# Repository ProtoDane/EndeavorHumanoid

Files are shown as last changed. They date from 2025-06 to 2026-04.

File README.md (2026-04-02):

# Endeavor II - 3D Printed Humanoid Robot
Endeavor II is a small scale humanoid robot with a height of 50 cm and 4 kg weight.  This robot is inspired by the Japanese robotics competition ROBO-ONE, and is capable of agile movements, combat-oriented sequences, and dance moves.  It is also designed to be fully 3D printed off standard commercial machines and use commercial off the shelf electronics.  Depending on shipping fees, the cost of this robot ranges between $600 to $800.

Endeavor II is fully open source.  In this repository you will find everythign you need to build and customize your own Endeavor: STEP, STL, and code files.

<p align="center">
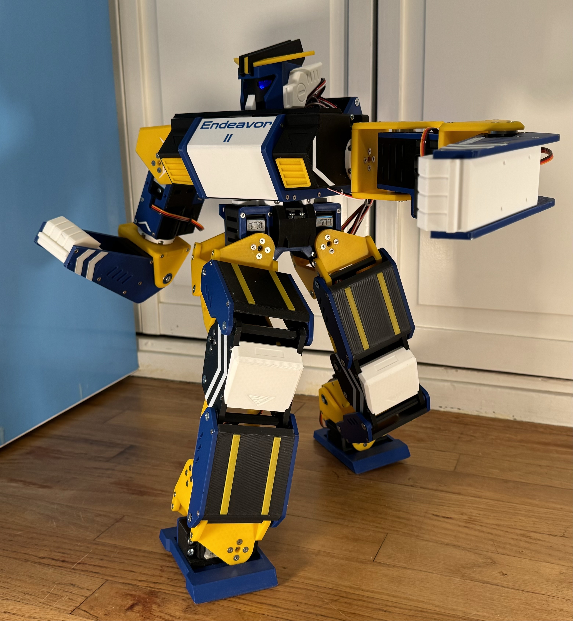
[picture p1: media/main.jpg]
  
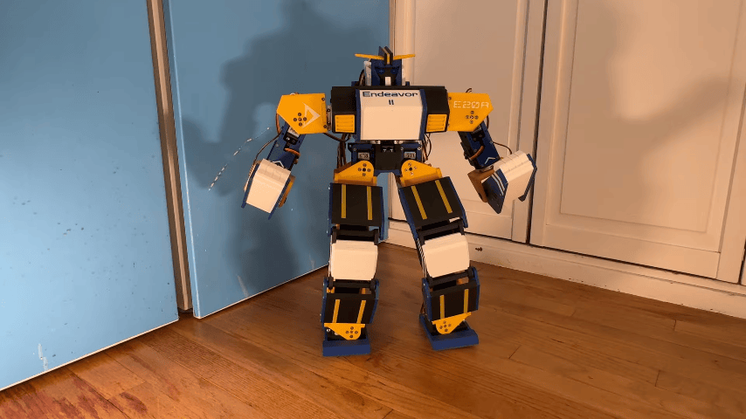
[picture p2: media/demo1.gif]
  
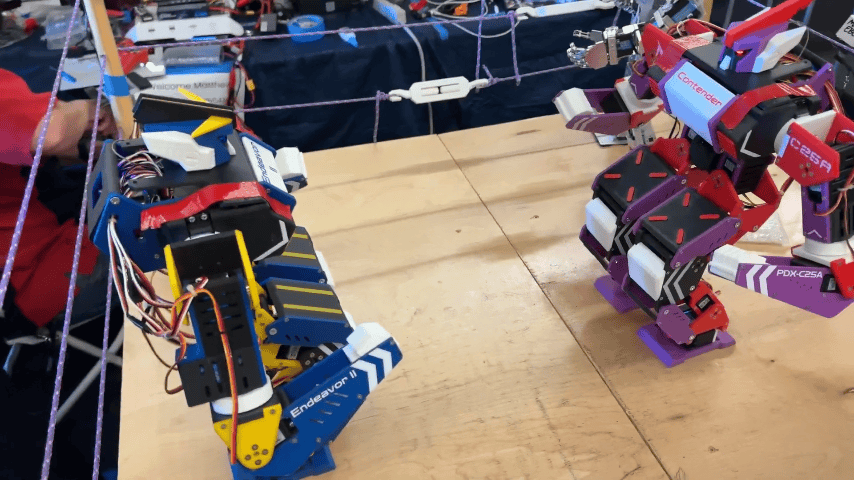
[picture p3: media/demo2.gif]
    
</p>

## Latest Update: (DATE)
**Initial Open Source Release!!!**

Version 01: Initial Open Source Release

See the [CHANGELOG.md] for full update history.

## Getting Started
### Installing this repository

Clone this repository to your local machine:
```bash
git clone
git submodule update --init --recursive
```

### Hardware Assembly

1. It is recommended to do the servo calibration before assemblying the robot.  Refer to [ServoCalibration.pdf] for instructions on how to do this.

1. Refer to [AssemblyDoc.pdf] for hardware assembly instructions.

1. Standard for wiring is in the works, but for now you can refer to the following wiring diagram:

<p align="center">
  
</p>

### Software Setup
Refer to [SoftwareSetup.pdf] for software setup instructions

## To-Do List
- [ ] Finish documentation
- [ ] ESP32 controller optimization (phase out ArduinoIDE code)
- [ ] ESPNOW support for PC teleoperation
- [ ] Idk do some cool stuff

## Support Me!

This project was created by ProtoDane Robotics.  If you like this project and wish to support my future works, I would really appreciate if you followed me on my [YouTube channel]!

If you wish to discuss this project with me, I have a [Discord server].

[STARTHERE.md]:./STARTHERE.md
[CHANGELOG.md]:./CHANGELOG.md
[Discord server]:https://discord.gg/Gm2sCxpUSx
[ServoCalibration.pdf]:./docs/ServoCalibration.pdf
[AssemblyDoc.pdf]:./docs/AssemblyDoc.pdf
[Youtube channel]:https://www.youtube.com/@ProtoDane

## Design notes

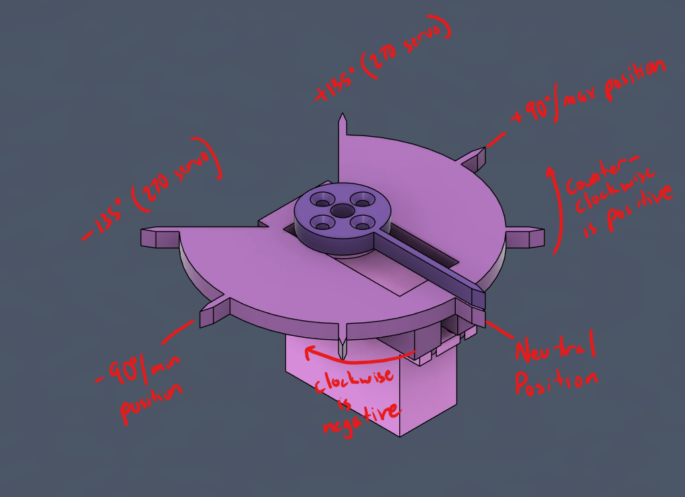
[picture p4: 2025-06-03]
media/servo_jig_annotate.png

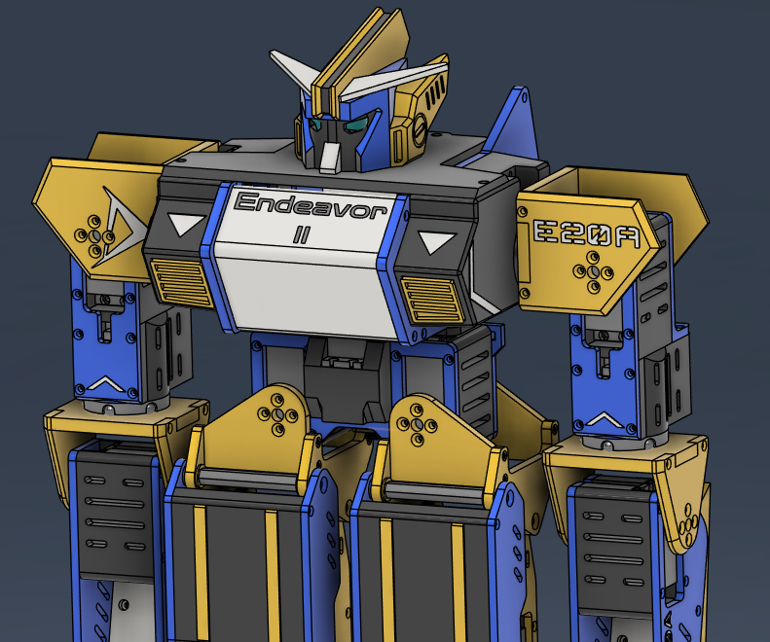
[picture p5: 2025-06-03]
media/Endeavor2_CAD.png

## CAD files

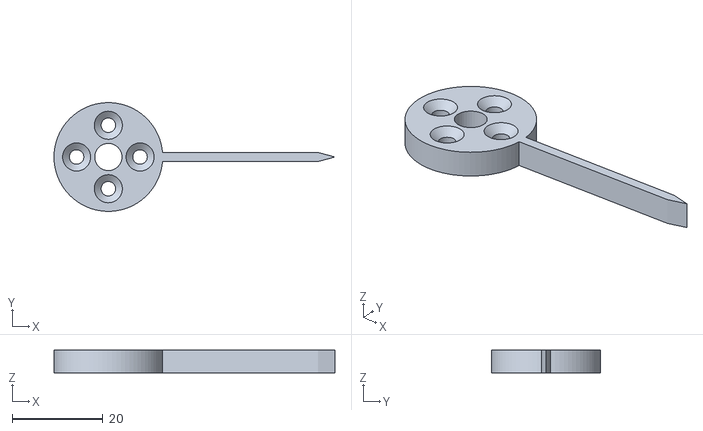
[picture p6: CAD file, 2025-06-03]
firmware/servo_calibration/ServoDial.stl
62.0 x 24.0 x 5.00

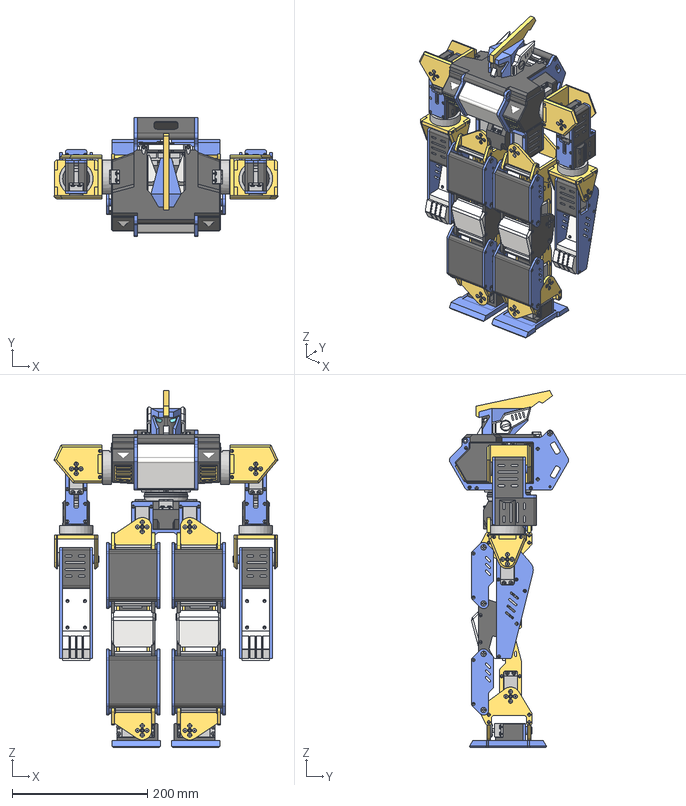
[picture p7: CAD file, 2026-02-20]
hardware/step files/EndeavorII-v1.step
331.0 x 176.6 x 527.7 mm
ElbowBaseBracket x 2
ElbowServoFlange x 2
ElbowBearingFlange x 2
91420A222_Steel Phillips Flat Head Screws x 38
8x14x4 Bearing x 12
ShaftPlug x 12
92010A020_NO THREADS_Passivated 18-8 Stainless Steel Phillips Flat He ad Screw x 241
92010A118_Passivated 18-8 Stainless Steel Phillips Flat Head Screw x 96
91290A111_Alloy Steel Socket Head Screw x 17
DS3235 Servo - Metal Horn x 17
ServoHousingA x 6
92005A118_NO THREADS_Steel Pan Head Phillips Screw x 68
FistBlock x 2
LeftForearmInnerPlate
LeftForearmOuterPlate
LeftShoulderRearFlange
ShoulderBracketBase x 2
LeftShoulderFrontFlange
BicepServoHousing x 2
ShoulderServoHousing x 2
BicepBracket x 2
RollsA x9 x 4
RollsB x9 x 4
ArmSlew-OuterRace x 4
ArmSlew-InnerBottom x 4
ArmSlew-InnerTop x 4
BicepPlate x 2
RightForearmOuterPlate
RightForearmInnerPlate
RightShoulderRearFlange
RightShoulderFrontFlange
TorsoBackPlate
TorsoLeftPlate
TorsoRightPlate
TorsoBottomPlate
RightVent
ShoulderHousingR
RightVent(Mirror)
ShoulderHousingL
TorsoTopCover
TorsoFrontCover
HeadBase
Helmet
Chinpiece
SidepieceL
SidepieceR
Horn
ElectronicsCarriage
Servo2040
Youngneer Single Chsnnel 5V Relay
IMU Mount
Zeee 2S Hard 5200mAh
switch-step
pcb
chip (1)
en button
boot button
usbport
Board
10uF x 2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

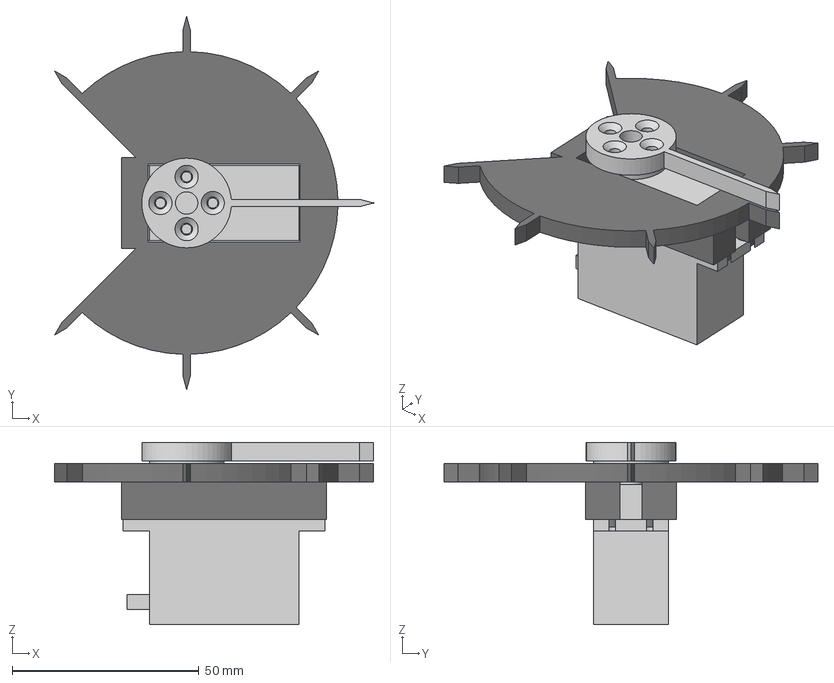
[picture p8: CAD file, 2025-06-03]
firmware/servo_calibration/ServoCalibrationJig.step
85.4 x 100.0 x 48.7 mm
DS3235 Servo - Metal Horn
ServoMount
ServoDial

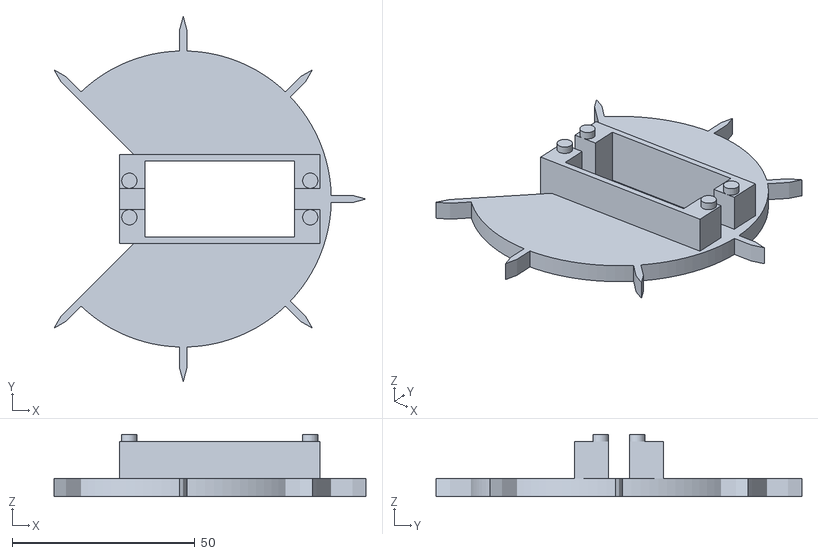
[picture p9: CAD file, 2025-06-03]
firmware/servo_calibration/ServoMount.stl
85.4 x 100.0 x 17.0

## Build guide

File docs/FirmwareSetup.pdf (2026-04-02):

# Programming Instructions

## For the Endeavor Humanoid by ProtoDane Robotics

## Requirements

- VSCode with PlatformIO
- (Optional) VS Code + Arm GNU Toolchain (mingw32) for working with the Servo2040; binary files and the communication protocol have been provided.

## 1: Flash the Servo 2040

Unless you want to add custom functionality, the binary files for the Servo 2040 have been provided to make the Pico SDK installs optional (this document does not cover the Servo2040 source code).

1. Download the binary file from the GitHub repository under servo2040/firmware/binaries. If using the Servo2040 without IMU, download servo2040_client.uf2. Otherwise, use servo2040_client_imu.uf2.
2. Plug in the Servo 2040 board to a computer via USB-C cable while holding down the BOOT button. Within a few seconds a file storage for the 2040 should pop up on the desktop.
3. Drag the .uf2 file into the 2040’s file storage. The file storage should disappear and LED lights should start coming up.

## 2: Configure the ESP32 code and upload

1. Open firmware/esp32_controller in VSCode and wait for PlatformIO to initialize and configure the project.
2. Find the MAC address of the Bluetooth controller you want to use for your robot and set that as the value of CTRL_MAC.

a. The MAC address of the Bluetooth controller can be found by running the ‘Controller’ sketch within the Bluepad32 Examples folder.
b. Upload the sketch to the ESP32 (or a spare one if you have it). Open the serial terminal (9600 baud rate).
c. Set your controller to pairing mode and wait for the connection message with the MAC address in the terminal.
3. Open platformio.ini and scroll down to [env:my_robot]. This is where you will configure your robot parameters; if you have multiple robots or different configurations, you should copy the lines including and below line 20.
a. CTRL_MAC: MAC Address of Bluetooth controller
b. IMU_CONFIG: 0 = IMU Disabled | 1 = BNO-055 | 2 = BNO-08X
c. SERIAL_DEBUG_MODE: If set true, disables all motor functions to safely troubleshoot over USB cable
d. FALL_PROTECTION_ENABLED: If set true, relay will automatically switch off when IMU_TIP_THRESHOLD (config.h) is reached
e. ULT_LOCK: If set true, will disable the tumble “ultimate” move for safety
f. CONFIG_FILE: If uncommented, will use the specified file name instead of robotInfoDefault.h
4. Navigate to robotInfoDefault.h (or your copied file). Fill in the servoStruct definitions with the servo calibration values that you recorded. The formatting is as follows: {min, mid, max, is180}, where is180 is a boolean value that is true of the servo is a 180-degree servo.
a. Example:

const servoStruct s_torso = {515, 1458, 2397, false}; | // TORSO
const servoStruct s_ra1 = | {510, 1495, 2397, false}; | // RIGHT ARM SHOULDER BASE
const servoStruct s_ra2 = | {543, 1505, 2413, false}; | // RIGHT ARM SHOULDER SWING
const servoStruct s_ra3 = | {592, 1495, 2404, true}; | // RIGHT ARM BICEP SWIVEL
const servoStruct s_ra4 = | {593, 1493, 2385, true}; | // RIGHT ARM ELBOW
const servoStruct s_rl1 = | {592, 1512, 2405, true}; | // RIGHT LEG THIGH
const servoStruct s_rl2 = | {588, 1490, 2372, true}; | // RIGHT UPPER LEG
const servoStruct s_rl3 = | {643, 1550, 2432, true}; | // RIGHT LOWER LEG
const servoStruct s_rl4 = | {587, 1493, 2405, true}; | // RIGHT LEG ANKLE
const servoStruct s_la1 = | {505, 1457, 2409, false}; | // LEFT ARM SHOULDER BASE
const servoStruct s_la2 = | {550, 1509, 2453, false}; | // LEFT ARM SHOULDER SWING
const servoStruct s_la3 = | {622, 1530, 2480, true}; | // LEFT ARM BICEP SWIVEL
const servoStruct s_la4 = | {622, 1533, 2440, true}; | // LEFT ARM ELBOW
const servoStruct s_ll1 = | {597, 1500, 2410, true}; | // LEFT LEG THIGH
const servoStruct s_ll2 = | {685, 1580, 2470, true}; | // LEFT UPPER LEG
const servoStruct s_ll3 = | {567, 1522, 2437, true}; | // LEFT LOWER LEG
const servoStruct s_ll4 = | {591, 1520, 2428, true}; | // LEFT LEG ANKLE

Note, you shouldn’t need to change the servoCluster mapping unless your servo wiring is different from the Wiring doc.

5. Plug in the ESP32 to your computer. Compile the project and upload.

## Sanity Checklist

After a few seconds the LED bar on the Servo2040 flashes green After a few seconds the LEDs inside the robot’s head flashes Pairing the Bluetooth controller to the robot is successful Pressing the Home Button brings the robot to its idle position

## Appendix A: Servo2040 Communication Protocol

- Servo2040 communicates with the ESP32 over UART1 at a baud rate of 115200
- Upon startup, the LED bar will light up to signal certain stages of the initialization process. The LED bar will flash all green to indicate that it is ready for operation.
- The Servo2040 will yield until the ESP32 sends a handshake message of 0b01101001 or a hexadecimal of 0x69 (this was not intentional, I swear).
- The Servo2040 waits for the ESP32 to receive a command byte, in which the leading 4 bits are known as the preamble; each value used to indicate what to send back to the

ESP32, however this feature has been deprecated. The Servo2040 will recognize the following bytes:
- 0x08
- 0x09
- 0x0F
- The trailing 4 bits of the command bit is the command code, and each value indicates an action the Servo2040 executes:
- 0x0F | CMD_ENABLE: Allows transmission of PWM signals to the servos.
- 0x01 | CMD_DISABLE: Discontinues sending PWM signals to the servos.
- 0x02 | CMD_LED: Controls the LED bar
■ The following byte controls which LEDs are lit. For instance, if the byte value is 0b10011, this indicates that LEDs 1, 2, and 5 are lit.
■ Example full message: (0x0F << 4 | CMD_LED) (0b10011)
- 0x07 | CMD_PULSE: Sends PWM signals to all servos
■ The command byte is followed by 36 bytes, each pair of bytes representing the target PWM pulse for a specific servo for a total of 18 actuators.
■ The pulse values must be between 500 and 2500 per manufacturing specifications. If the pulse value falls outside this range the servo will be ignored; this is implemented such that the user can control which servos need to be actuated.
■ Example message: (0x0F << 4 | CMD_PULSE) (10) (50) (0) (0) (15) (0)
(15) (0) (15) (0) […]
- Sets SERVO1 to 1050, ignores SERVO2, SERVO3-SERVO18 to 1500
- 0x06 | CMD_PULSE_DELAY: Moves all servos from current position to target
position within a specified time delay.
■ The command byte is followed by two bytes indicating the time delay in milliseconds, then the 36 bytes for the 18 servos.
■ Example message: (0x0F << 4 | CMD_PULSE_DELAY) (20) (50) [Same
parameters as CMD_PULSE]
- Moves all servos to desired position after 2050 ms
■ Note: speed of servos depend on the most recent pulse or delayed pulse command

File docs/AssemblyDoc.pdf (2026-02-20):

# Endeavor

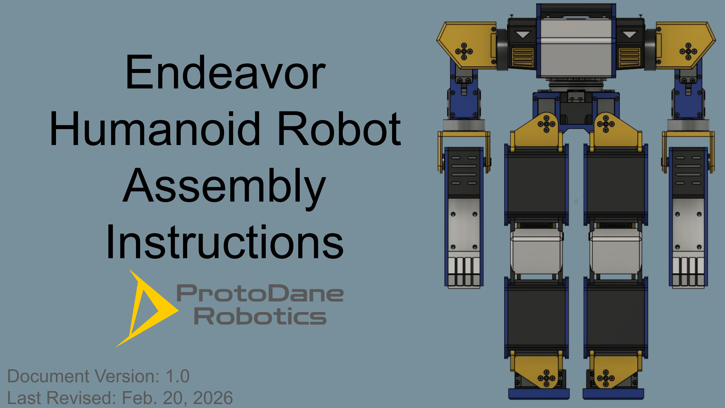
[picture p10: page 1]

# Humanoid Robot Assembly Instructions

# ProtoDane Robotics

## Document Version: 1.0 Last Revised: Feb. 20, 2026

# Notes

## - Refer to servo calibration instructions for DS3235 servos. All servos should be calibrated before starting assembly. Do not remove or rotate the servo

disc to ensure servo joints are set properly when powered.

## - This assembly does not contain heat inserts. As such, all fasteners should be tightened properly, either by hand or motorized tool. It is up to you to ensure that all fasteners are secured and not overtightened that it

destroys the printed hole.

## - Read each step carefully. You are responsible for proper assembly, safe tool handling, and any risks associated with this project. If you have any

questions, please reach out on the ProtoDane Discord server.

# 01: Ankle Servo Assembly

No. | Part Name | Qty
1 | LeftAnkleServoHousing | 1
2 | RightAnkleServoHousing | 1
3 | LeftAnkleBracket | 1
4 | RightAnkleBracket | 1
5 | DS3235 Servo | 2
6 | M3x8 Pan Head Screw | 8
7 | M2.5x10 Flat Head Screw | 6

7

6

5

2

1

3

4

# 02: Foot Mounting

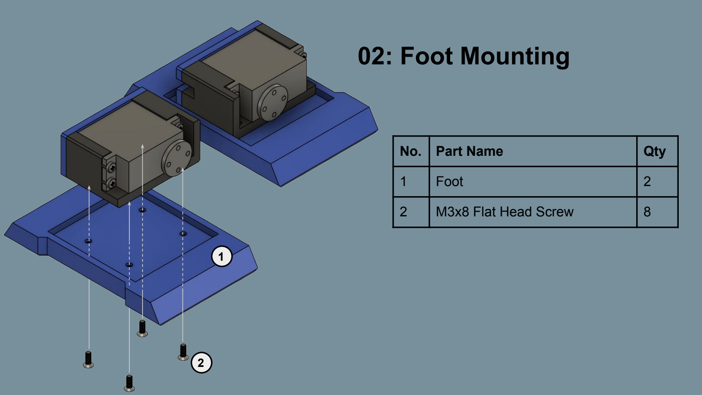
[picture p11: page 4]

No. | Part Name | Qty
1 | Foot | 2
2 | M3x8 Flat Head Screw | 8

1

2

# 03: Ankle Bracket Assembly

## *Repeat step

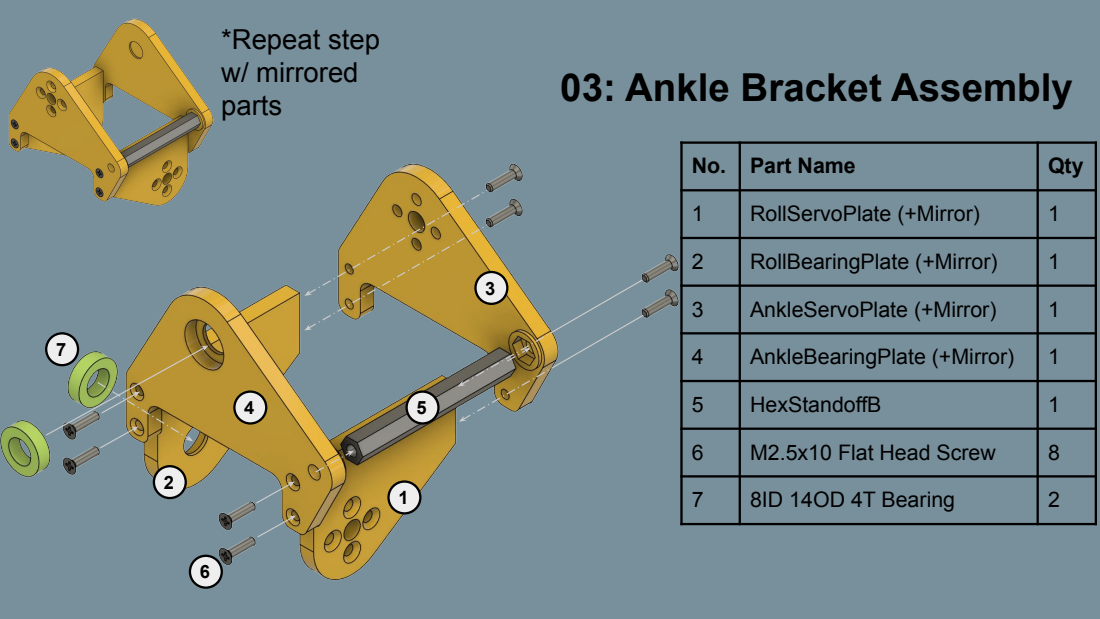
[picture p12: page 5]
Part Name; Qty; w/ mirrored parts

1 | RollServoPlate (+Mirror) | 1

2 | RollBearingPlate (+Mirror) | 1

3 | AnkleServoPlate (+Mirror) | 1

4 | AnkleBearingPlate (+Mirror) | 1

5 | HexStandoffB | 1

6 | M2.5x10 Flat Head Screw | 8

7 | 8ID 14OD 4T Bearing | 2

# 04: Thigh Bracket Assembly

## *Repeat step w/ mirrored parts

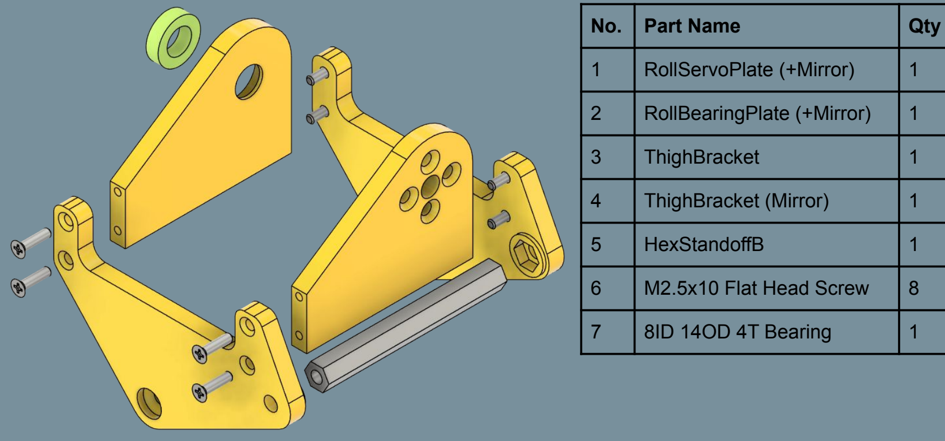
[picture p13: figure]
Part Name; Qty; RollServoPlate (+Mirror); RollBearingPlate (+Mirror); ThighBracket; ThighBracket (Mirror); HexStandoffB; M2.5x10 Flat Head Screw; 8ID 14OD 4T Bearing

# 05: Front Leg Guards

No. | Part Name | Qty
1 | FrontLinkage | 1(x4)
2 | FrontLinkage(Mirror) | 1(x4)
3 | FrontLinkageCover | 1(x4)
4 | M2.5x10 Flat Head Screw | 4(x4)

## *Build x4

1

2

3

4

# 06: Knee Assembly

## *Repeat step

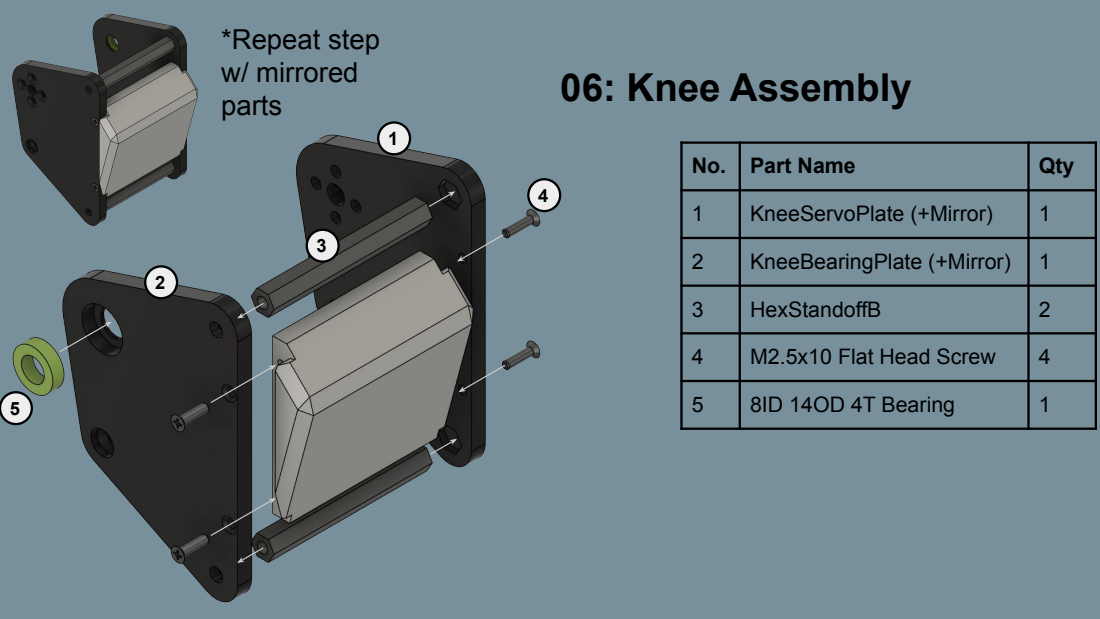
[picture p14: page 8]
w/ mirrored parts; Part Name; Qty 1; KneeServoPlate (+Mirror); KneeBearingPlate (+Mirror); HexStandoffB; M2.5x10 Flat Head Screw; 8ID 14OD 4T Bearing

# 07: Servo Module A

## *Build x6

No. | Part Name | Qty
1 | ServoHousingA | 1x6
2 | DS3235 Servo | 1x6
3 | M3x8 Pan Head Screw | 4x6
1

2

3

# 08: Servo Leg Assembly

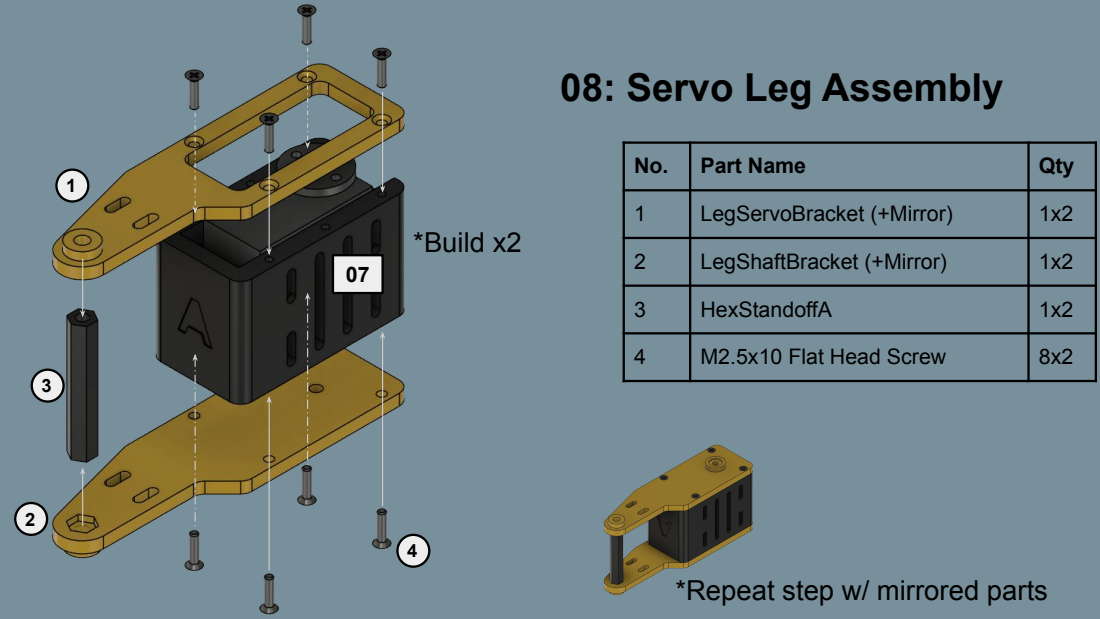
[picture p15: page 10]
*Build x2

No. | Part Name | Qty

1 | LegServoBracket (+Mirror) | 1x2

2 | LegShaftBracket (+Mirror) | 1x2

3 | HexStandoffA | 1x2

4 | M2.5x10 Flat Head Screw | 8x2

*Repeat step w/ mirrored parts

# 09a: Lower Leg Assembly

No. | Part Name | Qty
1 | M3x8 Flat Head Screw | 8
2 | M3x6 Socket Head Screw | 2
3 | M4x12 Flat Head Screw | 2
4 | ShaftSleeve | 2
Left leg pictured | Repeat step for right leg

08

03

02

1

2

3

4

## Install in the orientation as shown; this is the servo’s zero position

# 09b: Knee Mounting

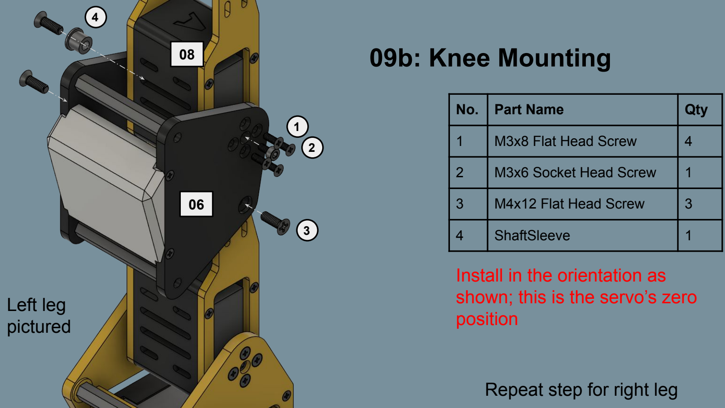
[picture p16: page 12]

No. | Part Name | Qty
1 | M3x8 Flat Head Screw | 4
2 | M3x6 Socket Head Screw | 1
3 | M4x12 Flat Head Screw | 3
4 | ShaftSleeve | 1

## Repeat step for right leg

## Left leg pictured

06

08

1

2

3

4

## Install in the orientation as shown; this is the servo’s zero position

# 09c: Thigh Bracket Mounting

No. | Part Name | Qty
1 | M4x12 Flat Head Screw | 2

## Repeat for right leg

## Left leg pictured

# 09d: Front Linkage Cover Mounting

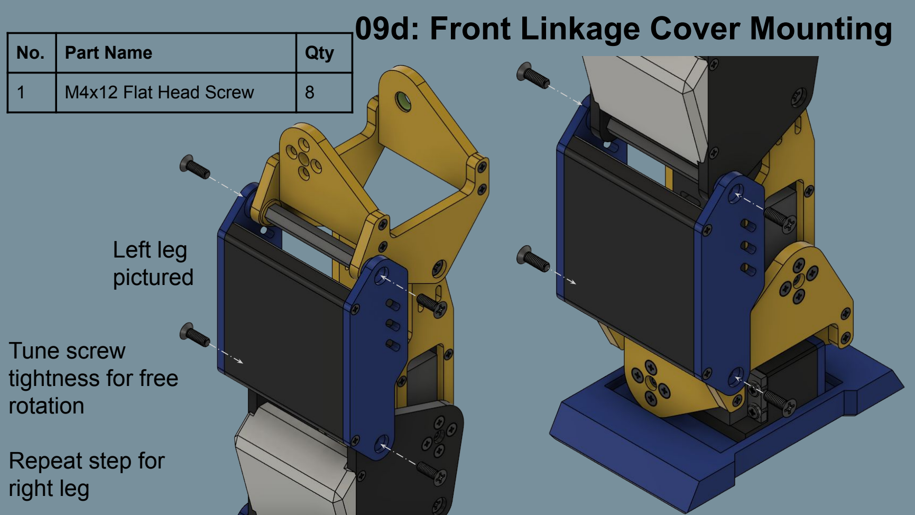
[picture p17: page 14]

No. | Part Name | Qty
1 | M4x12 Flat Head Screw | 8

## Tune screw tightness for free rotation

## Repeat step for right leg

## Left leg pictured

# 09e: Full Leg

Left Leg

Right Leg

# 10: Pelvis Servo Modules

No. | Part Name | Qty
1 | ThighServoHousing | 2
2 | TorsoServoHousing | 1
3 | DS3235 Servo | 3
4 | M3x8 Pan Head Screw | 12

## *Build x2

# 11: Pelvis Assembly

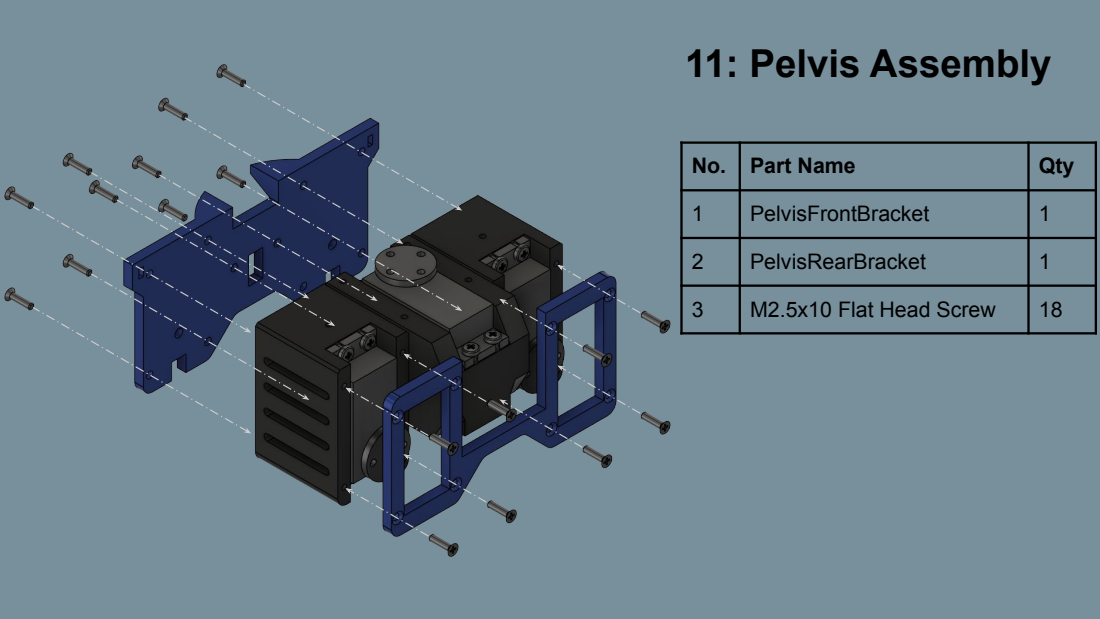
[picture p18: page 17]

No. | Part Name | Qty

1 | PelvisFrontBracket | 1

2 | PelvisRearBracket | 1

3 | M2.5x10 Flat Head Screw | 18

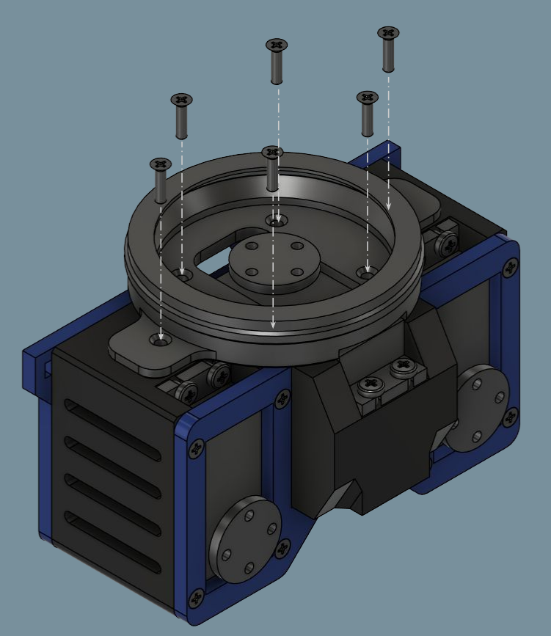
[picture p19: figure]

# 12a: Torso Slew Bearing Mounting

No. | Part Name | Qty
1 | TorsoSlew-OuterRace | 1
2 | M2.5x10 Flat Head Screw | 6

# 12b: Lower Cap + Rollers

No. | Part Name | Qty
1 | TorsoSlew-InnerBottom | 1
2 | SlewRoller | 26

## Drop the InnerBottom piece into the bearing

housing first.

## Alternate slew rollers by 90 degrees (see

image).

# 12c: Upper Cap Mounting

No. | Part Name | Qty
1 | TorsoSlew-InnerTop | 2
2 | M2.5x10 Flat Head Screw | 3
3 | M3x8 Flat Head Screw | 4
4 | M3x6 Socket Head Screw | 1

# 13: Pelvis/Leg Mounting

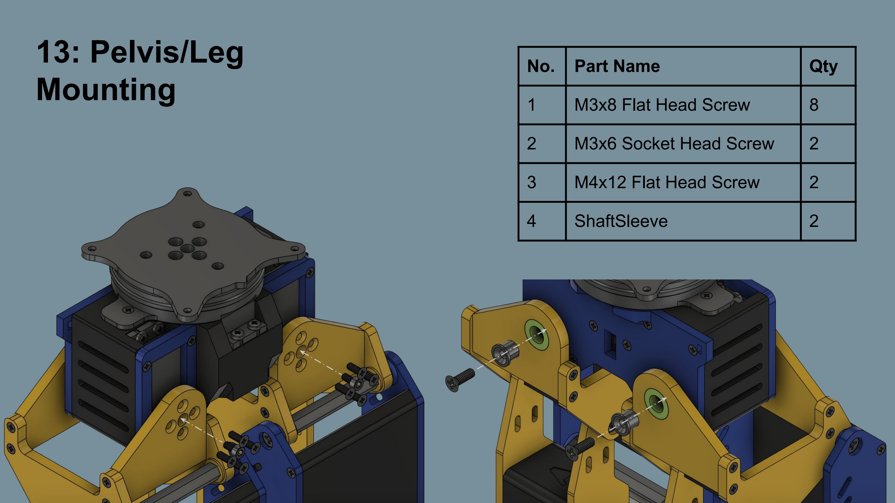
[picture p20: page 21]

No. | Part Name | Qty 1 | M3x8 Flat Head Screw | 8 2 | M3x6 Socket Head Screw | 2 3 | M4x12 Flat Head Screw | 2 4 | ShaftSleeve | 2

# 14a: Chest Servo Housing

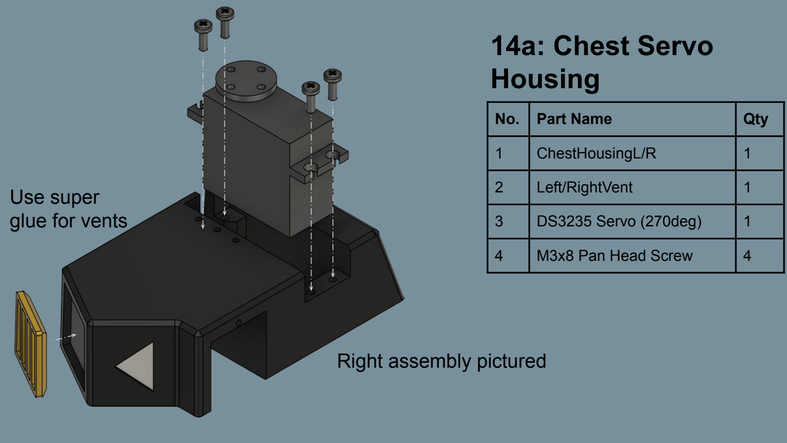
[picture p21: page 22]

No. | Part Name | Qty
1 | ChestHousingL/R | 1
2 | Left/RightVent | 1
3 | DS3235 Servo (270deg) | 1
4 | M3x8 Pan Head Screw | 4

## Right assembly pictured

## Use super glue for vents

# 14b: Arm Slew Bearing Mounting

No. | Part Name | Qty
1 | ArmSlew-OuterRace | 1
2 | M2.5x10 Flat Head Screw | 4*

## *3x screws okay if arranged in triangular pattern

## Right assembly pictured

# 14c: Lower Cap + Rollers

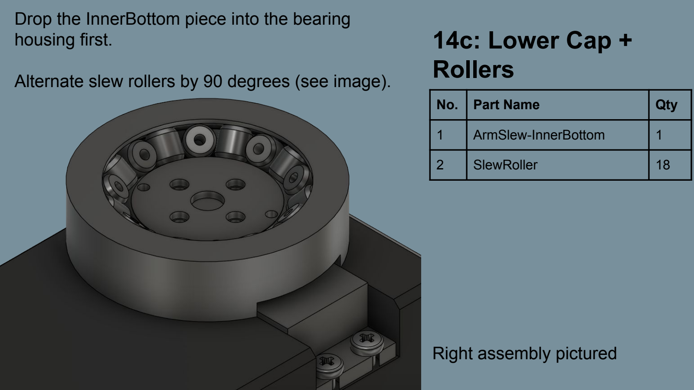
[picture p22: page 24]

No. | Part Name | Qty
1 | ArmSlew-InnerBottom | 1
2 | SlewRoller | 18

## Drop the InnerBottom piece into the bearing

housing first.

Alternate slew rollers by 90 degrees (see image).

## Right assembly pictured

# 14d: Upper Cap

No. | Part Name | Qty
1 | ArmSlew-InnerTop | 1
2 | M2.5x10 Flat Head Screw | 2
3 | M3x8 Flat Head Screw | 4
4 | M3x6 Socket Head Screw | 1

## Right assembly pictured

# 14e: Side Plate Mounting

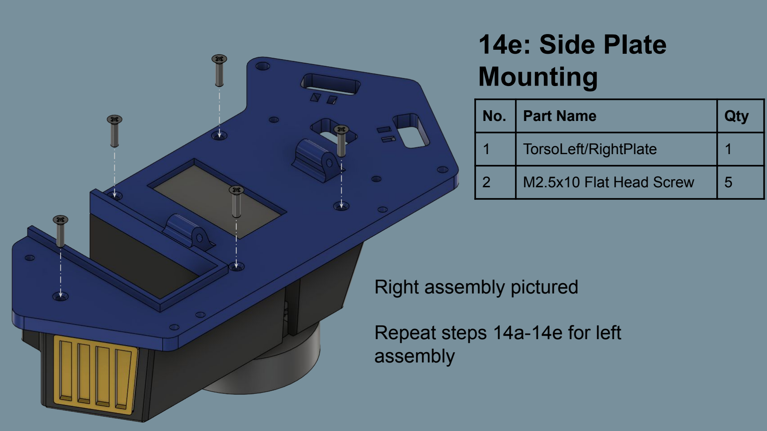
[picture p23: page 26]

No. | Part Name | Qty
1 | TorsoLeft/RightPlate | 1
2 | M2.5x10 Flat Head Screw | 5

## Right assembly pictured

## Repeat steps 14a-14e for left assembly

# 15a: Torso Bottom Plate Mounting

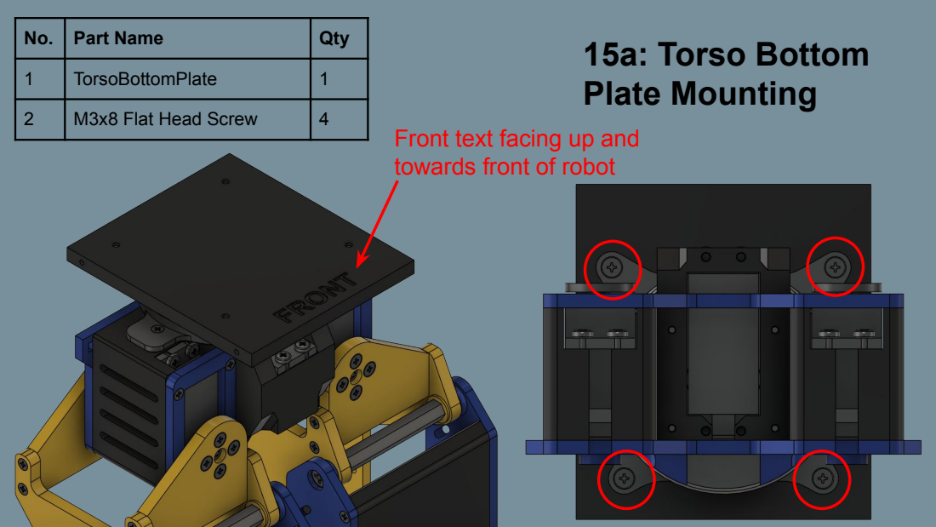
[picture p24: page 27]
M3x8 Flat Head Screw

No. | Part Name | Qty

1 | TorsoBottomPlate | 1

Front text facing up and
towards front of robot

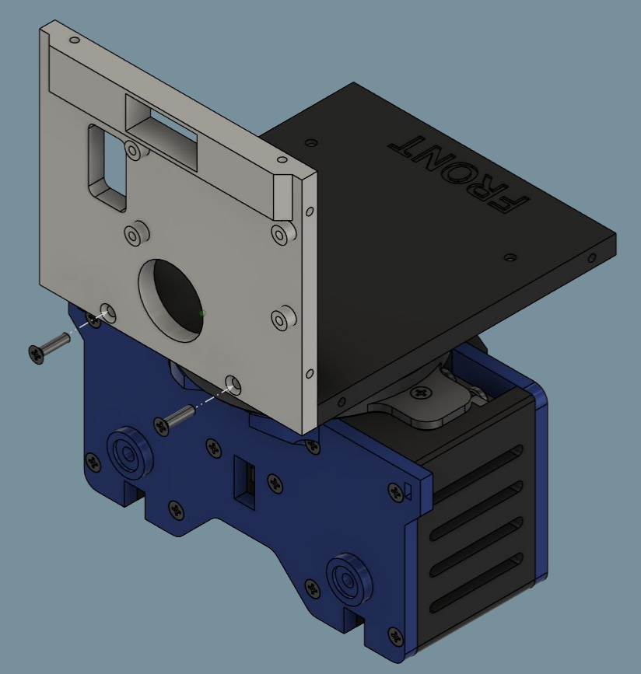
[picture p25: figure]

# 15b: Back Plate Mounting

No. | Part Name | Qty
1 | TorsoBackPlate | 1
2 | M2.5x10 Flat Head Screw | 2

# 15c: Side Assembly Mounting

No. | Part Name | Qty
1 | M2.5x10 Flat Head Screw | 4

## Repeat step for other side

# 15d: Back Cover Mounting

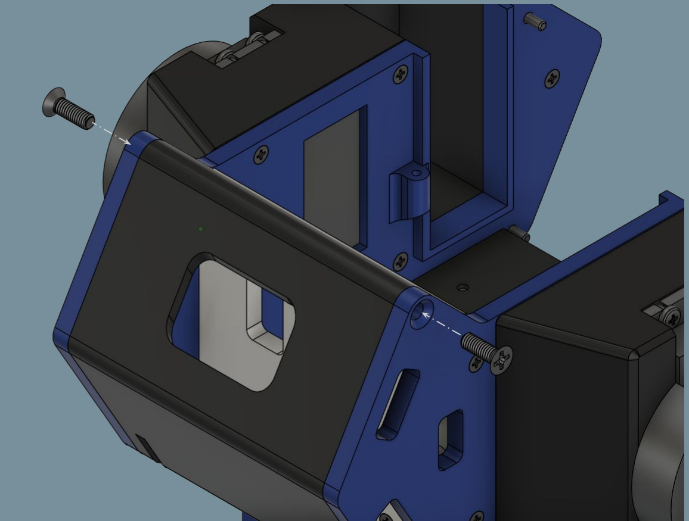
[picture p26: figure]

No. | Part Name | Qty
1 | BackCover | 1
2 | M4x12 Flat Head Screw | 2

# 15e: Front Cover Mounting

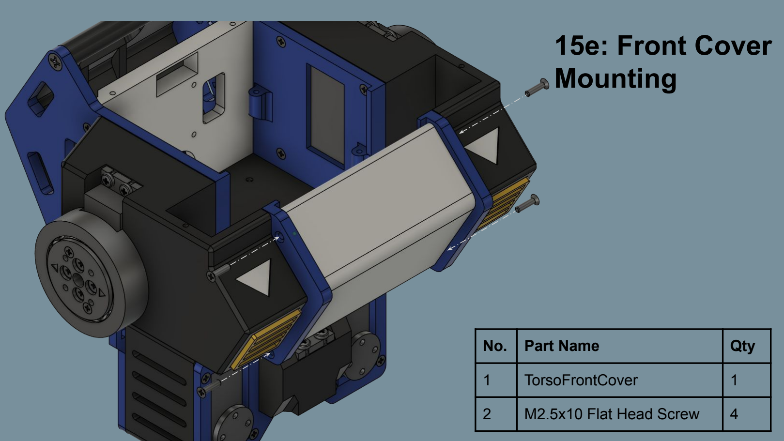
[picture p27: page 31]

No. | Part Name | Qty
1 | TorsoFrontCover | 1
2 | M2.5x10 Flat Head Screw | 4

# 16a: Top Torso Cover

No. | Part Name | Qty
1 | TorsoTopCover | 1
2 | HeadBase | 1
3 | Helmet | 1
4 | Chinpiece | 1
5 | SidepieceL | 1
6 | SidepieceR | 1
7 | Crest | 1

## Use super glue to secure all pieces

# 16b: Top Torso Cover

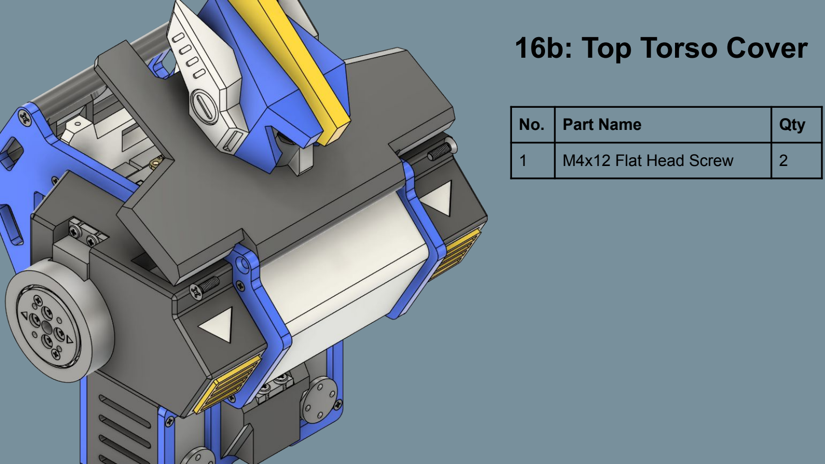
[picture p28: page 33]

No. | Part Name | Qty
1 | M4x12 Flat Head Screw | 2

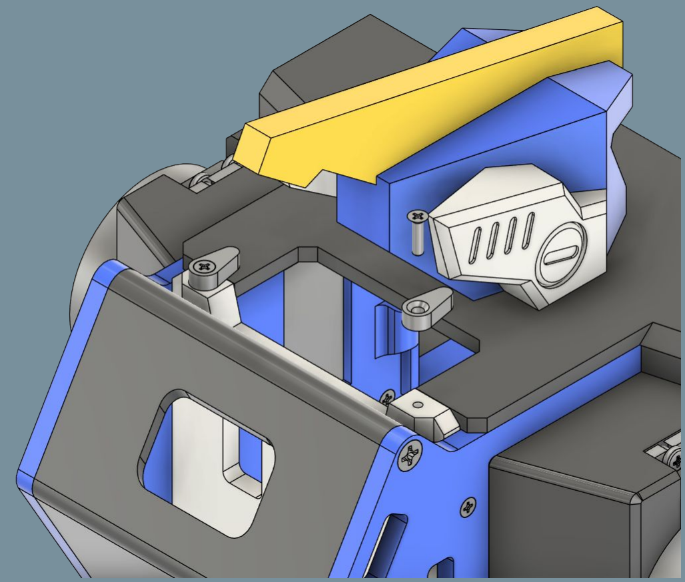
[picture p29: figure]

# 16c: Top Torso Cover

No. | Part Name | Qty
1 | LidStopper | 2
2 | M2.5x10 Flat Head Screw | 2

## Do not overtighten; lid stoppers must be able to

rotate to release the top cover, but not loose.

# 17a: Shoulder Brackets

No. | Part Name | Qty
1 | ShoulderBracketBase | 1
2 | Left/RightShoulderFrontFlange | 1
3 | Left/RightShoulderRearFlange | 1
4 | M2.5x10 Flat Head Screw | 4
5 | 8ID 14OD 4T Bearing | 1

## Right assembly pictured

## Repeat step for left assembly

# 17b: Bracket Mounting

No. | Part Name | Qty
1 | M3x8 Flat Head Screw | 4

## Repeat for other side

## Install in the orientation as shown; this is the servo’s zero position

# 18: Elbow Brackets

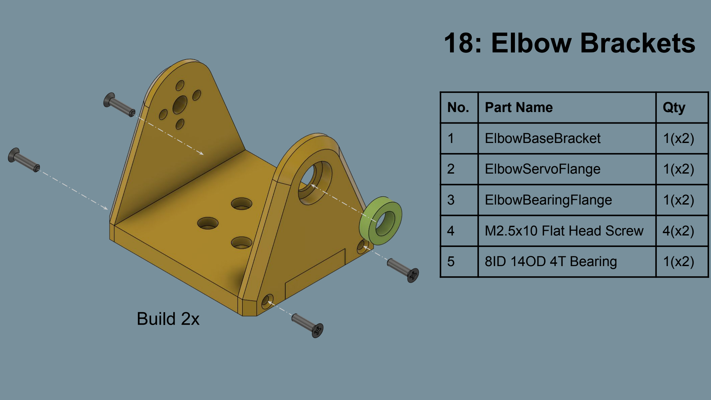
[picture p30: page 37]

No. | Part Name | Qty
1 | ElbowBaseBracket | 1(x2)
2 | ElbowServoFlange | 1(x2)
3 | ElbowBearingFlange | 1(x2)
4 | M2.5x10 Flat Head Screw | 4(x2)
5 | 8ID 14OD 4T Bearing | 1(x2)

## Build 2x

# 19a: Bicep Servo Housings

No. | Part Name | Qty
1 | ShoulderServoHousing | 1
2 | BicepServoHousing | 1
3 | DS3235 Servo | 2
4 | M3x8 Pan Head Screw | 8

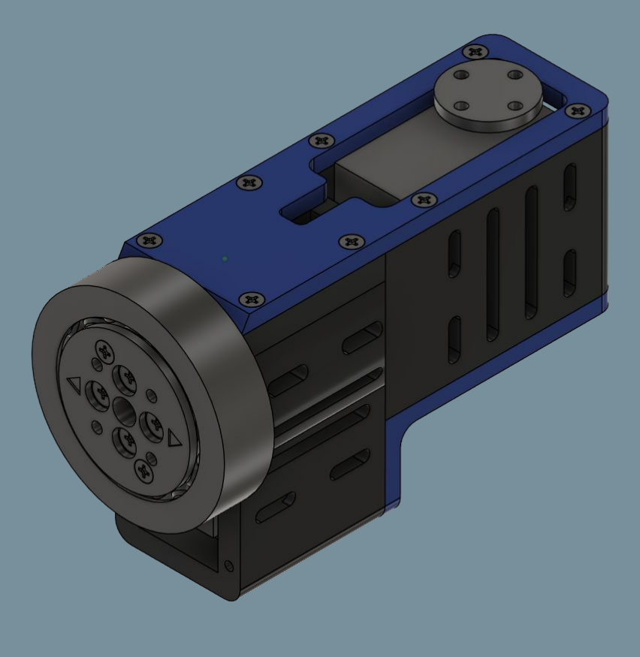
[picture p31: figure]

# 19c: Arm Slew Bearing

## Refer to 14b-14d for detailed steps

## Repeat steps 19a-19c

# 20: Forearm Assembly

No. | Part Name | Qty
1 | Left/RightForearmOuterPlate | 1
2 | Left/RightForearmInnerPlate | 1
3 | Fist | 1
4 | M2.5x10 Flat Head Screw | 14

## Left assembly pictured

## Repeat step for right assembly

# 21a: Elbow Bracket Mounting

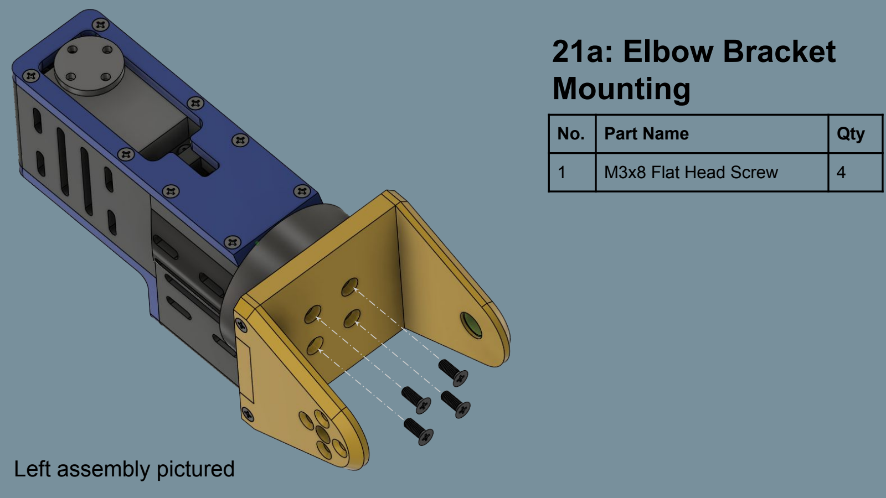
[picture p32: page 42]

No. | Part Name | Qty
1 | M3x8 Flat Head Screw | 4

## Left assembly pictured

# 21b: Forearm Mounting

No. | Part Name | Qty
1 | M3x6 Socket Head Screw | 1
2 | M3x8 Flat Head Screw | 4
3 | M4x12 Flat Head Screw | 1
4 | ShaftSleeve | 1

## Left assembly pictured

## Install in the orientation as shown; this is the servo’s zero position

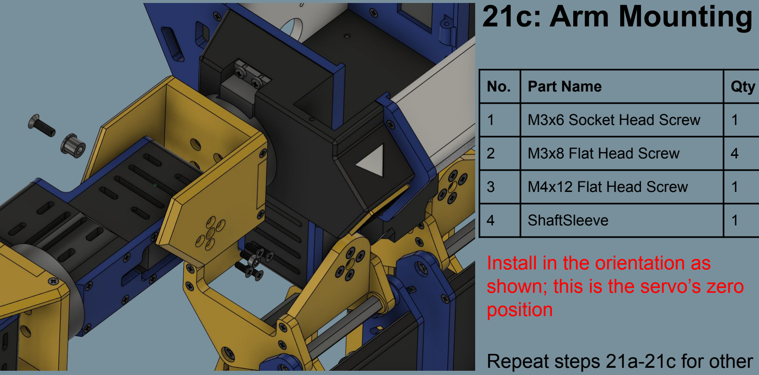
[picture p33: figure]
21c: Arm Mounting; Install in the orientation as shown; this is the servo’s zero position; Part Name; Qty; M3x6 Socket Head Screw; M3x8 Flat Head Screw; M4x12 Flat Head Screw; ShaftSleeve; Repeat steps 21a-21c for other

## side

## ❏ All joints are structurally stable with minimal wobble and resistance (with

exception of motor torque).

## ❏ All joints have been fastened, preferably with reinforcement from a thread

bonding agent (e.g. Loctite) to prevent the servo joint from becoming loose.

## ❏ All structural components are fastened properly with no noticeable gaps

between component interfaces.

# Sanity Checklist

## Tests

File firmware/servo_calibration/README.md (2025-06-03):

# Servo Calibration
I created a simple tool to map the servo PWM values (in microseconds) and map them to angular positions.  This was created because a problem I noticed with Endeavor I was that the servos did not behave the same way.  

When you control a servo, you're often calling servo.write(angle) or an equivalent in other platforms.  What's really going on is that the angle is converted to a pulse width value, which is what's actually sent as a signal to the servo.  However, this convertion is based on an assumed mapping.  Due to things like product quality and manufacturing variations, what may be considered as "45 degrees" may vary by as large as 200 usec pulse difference.

As such, I've designed a jig that consists of a servo dial and an angle measurement indicator.  We use this with the servo_calibration.ino code that I wrote in order to map the intended angles to their actual pulse values.

## Requirements
* Arduino (doesn't matter what model, just needs to work!)
* Serial terminal, PuTTY preferred for live key input
* Servo
* Servo Horn ([Use this] or something of equivalent dimensions)

[Use this]:https://www.amazon.com/dp/B07D56FVK5?ref_=ppx_hzsearch_conn_dt_b_fed_asin_title_2

## Wiring
Nothing too crazy, just hook up the servo to the Arduino's D7 and GND, then wire the servo to an external PSU set to servo voltage (typically 7.4v).



## Instructions
1. Mount 3D printed jig parts to servo, the servo jig goes down from the top (be sure the servo axis is centered), and the servo dial takes in M3 bolts (flathead preferred)
2. Turn on PSU, set voltage to servo range, and connect to servo
3. Plug in USB from your computer to Arduino and open up the serial terminal
4. Follow the instructions in the terminal...
    * Physically adjust the servo horn so that the dial is as close to the neutral position as possible
    * Using the terminal, move the servo so that the dial is at neutral position (~1500 usec); Press SPACE to confirm
    * Using the terminal, move the servo so that the dial is at max position (+90/~2500 usec); Press SPACE to confirm
    * Using the terminal, move the servo so that the dial is at min position (-90/~500  usec); Press SPACE to confirm
    * Run a sanity check by using the terminal to control the servo angle (calibrates to the mapped pulse value automatically).  Check with the jig markings to make sure mostly everything lines up (NOTE: RC servos are inherently unfit for high precision robotics, so expect some error.  At the very least your neutral and min/max values should be accurate)
    * Record the neutral and min/max calibration values (you might want to label the servos as well to keep track).  These will be used to write the robot's firmware.



## Other Notes
* If you're calibrating a 270-degree servo, the instructions are the same, but instead of +/- 90 deg as the min/max, calibrate to the +/- 135 deg marks (one jig mark further).  When running the sanity check, 30 degrees in the terminal correspond to 45 degrees on the servo; the code was made for 180 degrees, which make up the majority of servos, thus didn't justify accommodating for both.

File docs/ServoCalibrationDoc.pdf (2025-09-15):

Last Updated: 2025-09-15

# Servo Calibration Instructions

## For the Endeavor Humanoid Robot by ProtoDane Robotics

## Required Materials:

- Servo Calibration Jig (Servo Dial / Servo Mount)
- DS3235 Servo + Metal Disc
- 2x M3 Screws
- Arduino (Uno, Nano, etc.)
- Power Station

## 1: Prepare the Electronics Setup

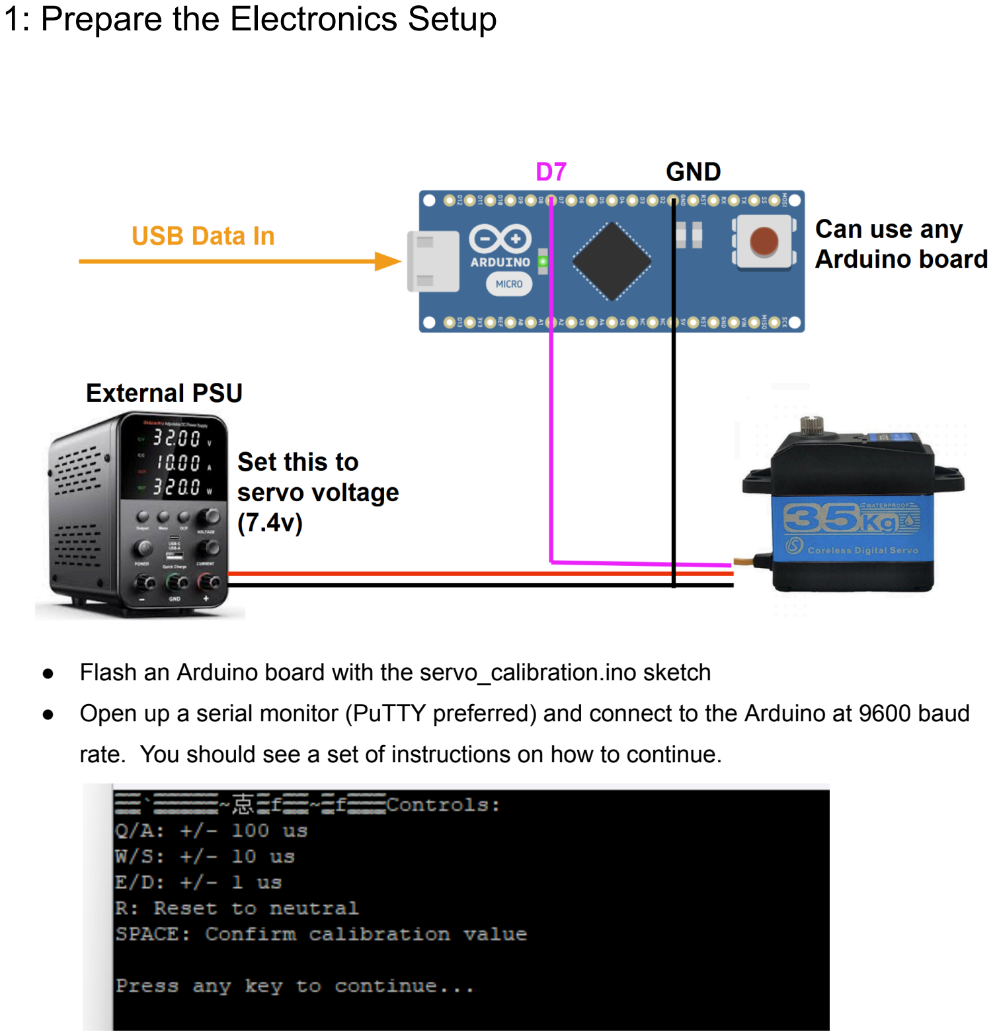
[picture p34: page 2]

- Flash an Arduino board with the servo_calibration.ino sketch
- Open up a serial monitor (PuTTY preferred) and connect to the Arduino at 9600 baud rate. You should see a set of instructions on how to continue.

## 2: Set up Servo in Jig

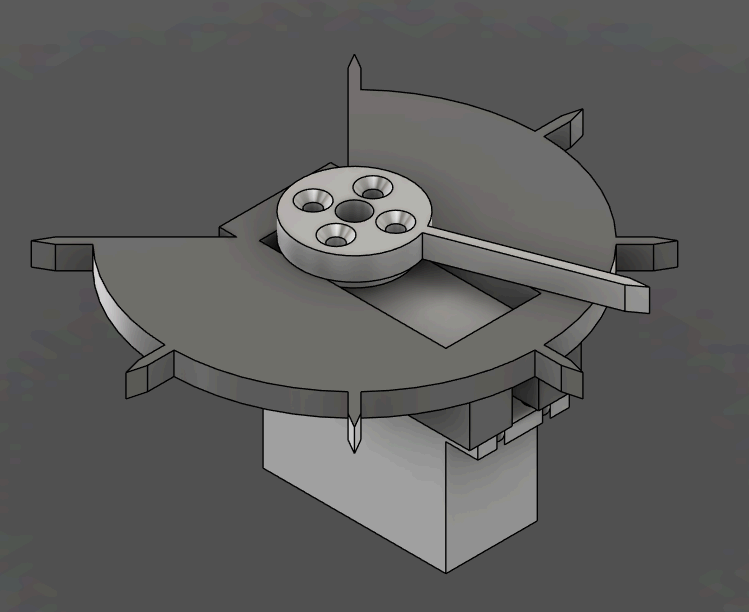
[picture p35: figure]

1. Pop in the ServoMount piece, which should plug into the holes on the mounting tabs of the servo motor.
2. Install the servo disk and fasten the ServoDial piece to the disk using 4x M3x8 Screws (Flathead preferred).

## 3: Calibrate the Servo

The following steps are to be done for the 17 servos prior to installation on the robot:

1. Start the calibration process on the serial terminal. The servo should move to the middle position (1500 usec). Remove and reposition the dial/disk from the servo shaft so that it is as close to the middle mark as possible. Beyond this step the dial and horn should not be detached from the servo.
2. Using the terminal, adjust the dial over the middle mark on the jig. This value will be between 1400 and 1600 usec. Press SPACE to confirm.

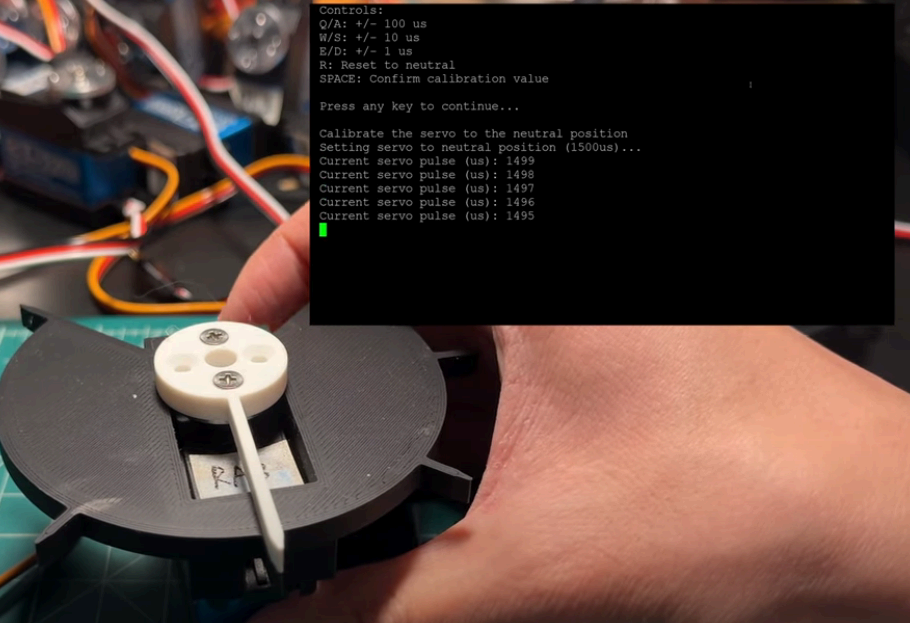
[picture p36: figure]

3. Using the terminal, move the dial to the maximum position (counter-clockwise from neutral). This value will be between 2300 and 2500 usec. Press SPACE to confirm. Note: The markings on the jig are at 45-degree increments. The max point for 180-degree servos is 90-degrees, and that for 270-degree servos is 135-degrees. Please keep this in mind!

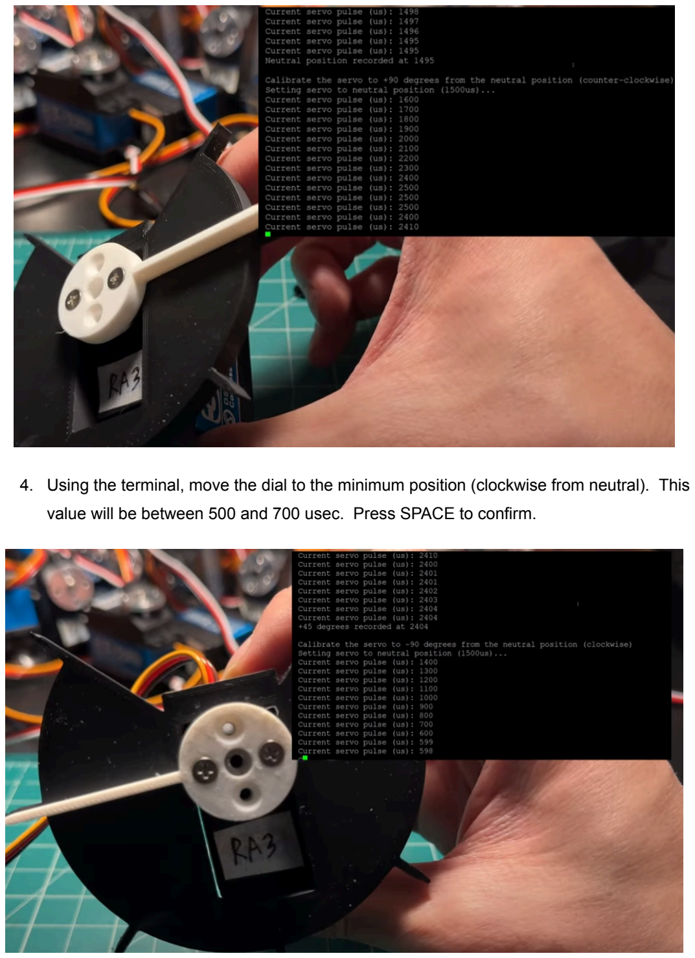
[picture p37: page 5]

4. Using the terminal, move the dial to the minimum position (clockwise from neutral). This value will be between 500 and 700 usec. Press SPACE to confirm.

5. Run a sanity check by using the terminal to control the servo angle (the angle will be mapped to the calibrated pulse). Check with the jig markings to make sure the readings are accurate and press SPACE. Note: RC servos tend to have non-linear pulse-to-angle relation, so expect some deviations especially with the 45-degree tick marks. At the very least make sure that the min/max/mid positions are correct.
6. Record the results of the calibration, which should be printed to the serial terminal after completing the sanity check. It is recommended to assign the servo a unique ID and label it on the top surface. See Page [X] for a sample worksheet.
7. Move the servo dial back to the neutral position. Remove the servo from the jig, careful not to remove the metal disk from the servo. With the servo disk still at the neutral position, mark the top surface in case the disk rotates out of position.

## Servo Calibration Worksheet

ID | Position | Mid | Max | Min
TORSO | Torso
RA1 | Right Shoulder Pitch
RA2 | Right Shoulder Roll
RA3 | Right Forearm Swivel
RA4 | Right Elbow
RL1 | Right Thigh
RL2 | Right Upper Leg
RL3 | Right Lower Leg
RL4 | Right Ankle
LA1 | Left Shoulder Pitch
LA2 | Left Shoulder Roll
LA3 | Left Forearm Swivel
LA4 | Left Elbow
LL1 | Left Thigh
LL2 | Left Upper Leg
LL3 | Left Lower Leg
LL4 | Left Ankle

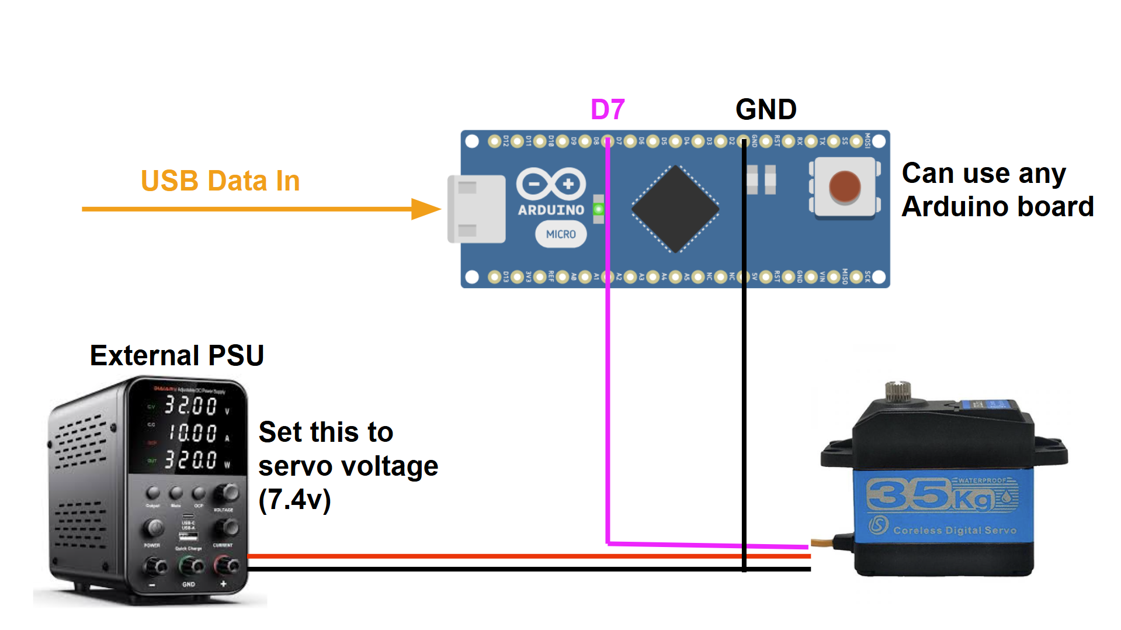
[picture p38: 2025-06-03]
media/servo_calibration_wiring.png

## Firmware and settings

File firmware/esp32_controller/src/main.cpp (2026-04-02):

// Include System libraries
#include <Arduino.h>
#include <uni.h>
#include <Bluepad32.h>
#include <PID_v1.h>
#include <Adafruit_BNO08x.h>

// Include User-Defined Libraries
#include "imu.h"
#include "servo2040.h"
#include "systemParams.h"
#include "config.h"
#include "actions.h"

HardwareSerial IMUSerial(1);
HardwareSerial servoSerial(2);
Adafruit_BNO08x bno08x(-1);

// Control variables
bool operable = true;
bool enableBalancing = false;
volatile bool relayState = false;
volatile bool tipSafetyEnabled = false;
bool isIdle = false;

// PID
double Kp = 1.0; // go lower
double Ki = 0.0;
double Kd = 0.02;
double pidSet, pidIn, pidOut;
PID pidPitch(&pidIn, &pidOut, &pidSet, Kp, Ki, Kd, DIRECT);

// Dual core instances
TaskHandle_t imuTaskHandle;
TaskHandle_t serialTaskHandle;
QueueHandle_t imuQueue;
QueueHandle_t serialQueue;

// User-defined handler objects
servoHandler servo;
imuHandler imu;
actionHandler actions;

ControllerPtr myControllers[BP32_MAX_CONTROLLERS];

// ==========================================================================
// Helper Functions
// ==========================================================================

// Schedules messages by bytes to be sent to the Servo2040 via UART 
void queueSerial(int input) {
    xQueueSend(serialQueue, &input, 0);
}

// Schedules messages to be sent to the serial console (non-blocking)
void queueConsole() {

}

// ==========================================================================
// Bluepad32 Handler Functions
// ==========================================================================

// Handler for controller connected event
void onConnectedController(ControllerPtr ctl) {
  
    bool foundEmptySlot = false;
    for (int i = 0; i < BP32_MAX_GAMEPADS; i++) {
        
        if (myControllers[i] == nullptr) {
        
        myControllers[i] = ctl;
        foundEmptySlot = true;

        // Optional, once the gamepad is connected, request further info about the
        // gamepad.
        ControllerProperties properties = ctl->getProperties();
        char buf[80];
        sprintf(buf,
            "BTAddr: %02x:%02x:%02x:%02x:%02x:%02x, VID/PID: %04x:%04x, "
            "flags: 0x%02x",
            properties.btaddr[0], properties.btaddr[1], properties.btaddr[2],
            properties.btaddr[3], properties.btaddr[4], properties.btaddr[5],
            properties.vendor_id, properties.product_id, properties.flags);
        // Serial.println(buf);

        break;
        }
    }
  
    if (!foundEmptySlot) {
        Serial.println("CALLBACK: Controller connected, but could not found empty slot");
    }
}

// Handler for controller disconnected event
void onDisconnectedController(ControllerPtr ctl) {
    bool foundGamepad = false;

    for (int i = 0; i < BP32_MAX_GAMEPADS; i++) {
        
        if (myControllers[i] == ctl) {
        // Serial.print("CALLBACK: Controller is disconnected from index=");
        // Serial.println(i);
        myControllers[i] = nullptr;
        foundGamepad = true;
        break;
        }
    }

    if (!foundGamepad) {
        // Serial.println("CALLBACK: Controller disconnected, but not found in myControllers");
    }
}

// Decision Tree based on gamepad input
void gamepadProcessor(ControllerPtr gamepad) {
    
    // Check home button state and determine if a debounce action occurs and toggles the relay
    if (gamepad->miscSystem() & operable) {

        while(gamepad->miscSystem()) {BP32.update(); delay(50);}

        relayState = !relayState;

        if (!SERIAL_DEBUG_MODE) {
            digitalWrite(RELAY_PIN, !digitalRead(RELAY_PIN));
            digitalWrite(HEAD_PIN, !digitalRead(HEAD_PIN));
        }

        relayState ? servo.cmdEnable() : servo.cmdDisable();
    }

    // Check relay state and process the remaining gamepad controls if it is high
    if (relayState) {

        // Fetch left/right joystick values
        int lx = gamepad->axisX();
        int ly = gamepad->axisY();
        int rx = gamepad->axisRX();
        int ry = gamepad->axisRY();
        
        // Check buttons first, then check drive controls last.  If no inputs, send idle command to servo driver
        if (gamepad->a()) {
        
            // Serial.println("[ESP32]: (B) pressed");
            tipSafetyEnabled = true;
            isIdle = false;
            actions.actionCrouch(gamepad);

        } else if (gamepad->b()) {

            // Serial.println("[ESP32]: (A) pressed");
            tipSafetyEnabled = true;
            isIdle = false;
            actions.actionSwipe(gamepad, false);
        
        } else if (gamepad->y()) {

            // Serial.println("[ESP32]: (X) pressed");
            if(!ULT_LOCK) {
                tipSafetyEnabled = false;
                actions.actionTumble(gamepad);
                tipSafetyEnabled = true;
                isIdle = false;
            }
        
        } else if (gamepad->x()) {

            // Serial.println("[ESP32]: (Y) pressed");
            tipSafetyEnabled = true;
            isIdle = false;
            actions.actionSwipe(gamepad, true);
        
        } else if (gamepad->dpad() & DPAD_UP) {

            // Serial.println("[ESP32]: DP-UP pressed");
            tipSafetyEnabled = true;
            isIdle = false;
            actions.emoteHero(gamepad);
        
        } else if (gamepad->dpad() & DPAD_DOWN) {

            // Serial.println("[ESP32]: DP-DOWN pressed");
            //actionEmote2(gamepad);
            tipSafetyEnabled = true;
            isIdle = false;
            actions.emoteGangnam(gamepad);

        } else if (gamepad->dpad() & DPAD_LEFT) {
        
            // Serial.println("[ESP32]: DP-LEFT pressed");
            tipSafetyEnabled = true;
            isIdle = false;
            actions.emoteShikanoko(gamepad);

        } else if (gamepad->dpad() & DPAD_RIGHT) {

            // Serial.println("[ESP32]: DP-RIGHT pressed");
            tipSafetyEnabled = true;
            isIdle = false;
            actions.emoteTaunt(gamepad);

        } else if (gamepad->l1()) {
        
            // Serial.println("[ESP32]: L-Shoulder pressed");
            tipSafetyEnabled = true;
            isIdle = false;
            actions.actionPunch(gamepad, true);
        
        } else if (gamepad->l2()) {  
        
            // Serial.println("[ESP32]: L-Trigger pressed");
            tipSafetyEnabled = true;
            isIdle = false;
            actions.actionUpperCut(gamepad, true);
        
        } else if (gamepad->r1()) {
        
            // Serial.println("[ESP32]: R-Shoulder pressed");
            tipSafetyEnabled = true;
            isIdle = false;
            actions.actionPunch(gamepad, false);
        
        } else if (gamepad->r2()) {
        
            // Serial.println("[ESP32]: R-Trigger pressed");
            tipSafetyEnabled = true;
            isIdle = false;
            actions.actionUpperCut(gamepad, false);
        
        // } else if (gamepad->thumbL()) {
        // } else if (gamepad->thumbR()) {
        // } else if (gamepad->miscBack()) {   // (-) Button Pressed

        } else if (gamepad->miscHome()) {   // (+) Button Pressed

            // actionGetupFront(gamepad);
            actions.actionGetup(gamepad);
            isIdle = false;
            tipSafetyEnabled = true;

        } else if (ly < -AXIS_THRESHOLD || ry < -AXIS_THRESHOLD) {
        
            Serial.println("[ESP32]: Walk forward");
            tipSafetyEnabled = true;
            isIdle = false;
            actions.moveWalkFwd(gamepad);
        
        } else if (ly > AXIS_THRESHOLD || ry > AXIS_THRESHOLD) {  
        
            Serial.println("[ESP32]: Walk backward");
            tipSafetyEnabled = true;
            isIdle = false;
            actions.moveWalkBwd(gamepad);
        
        } else if (lx > AXIS_THRESHOLD) {
        
            Serial.println("[ESP32]: Spin right");
            tipSafetyEnabled = true;
            isIdle = false;
            actions.moveSpin(gamepad, false);
        
        } else if (lx < -AXIS_THRESHOLD) {

            Serial.println("[ESP32]: Spin left");
            tipSafetyEnabled = true;
            isIdle = false;
            actions.moveSpin(gamepad, true);
    
        } else if (rx < -AXIS_THRESHOLD) {

            Serial.println("[ESP32]: Strafe left");
            tipSafetyEnabled = true;
            isIdle = false;
            actions.moveStrafe(gamepad, true);
        
        } else if (rx > AXIS_THRESHOLD) {

            Serial.println("[ESP32]: Strafe right");
            tipSafetyEnabled = true;
            isIdle = false;
            actions.moveStrafe(gamepad, false);
        
        } else {
            // Serial.println("IDLE");
            // if (!isIdle) {
            //     actions.actionIdle();
            //     isIdle = !isIdle;
            // }
            actions.actionIdle();
        }


    }
}

// ==========================================================================
// FreeRTOS tasks
// ==========================================================================

// Processing task for sending and receiving data to/from the Servo2040 via UART serial
// Priority 3 | Core 0
void servoSerialTask(void *params) {

    double filteredPitch = 0.0;
    int input;
    enum {READ_CMD, READ_IMU} state = READ_CMD;
    uint8_t buffer[24];
    bool loopContents = false;

    while(1) {
        
        loopContents = false;

        if (xQueueReceive(serialQueue, &input, 0) == pdTRUE) {
            Serial.println(input);
            servoSerial.write(input);
            loopContents = true;
        }

        if (state == READ_CMD) {
            // Read one byte for command
            if (servoSerial.available() > 0) {
                if (servoSerial.read() == 0b10010000) {
                    state = READ_IMU;
                    loopContents = true;
                }
            }
        } else if (state == READ_IMU) {
            // Read 24 bytes for IMU buffer
            if (servoSerial.available() >= 24) {
                servoSerial.readBytes(buffer, 24);
                state = READ_CMD;

                queueBin msg;
                memcpy(&msg.eulerX, &buffer[0], 8); // roll
                memcpy(&msg.eulerY, &buffer[8], 8); // pitch
                memcpy(&msg.eulerZ, &buffer[16], 8); // yaw

                filteredPitch = 0.5 * msg.eulerY + (1 - 0.5) * filteredPitch;
                pidIn = filteredPitch;
                pidSet = 0;
                pidPitch.Compute();
                msg.pidOut = pidOut;
                msg.dX = 125.0 * tan(radians(pidOut));
                
                xQueueOverwrite(imuQueue, (void *) &msg);

                // Serial.println(msg.dX);

                if (tipSafetyEnabled && abs(filteredPitch) > IMU_TIP_THRESHOLD && FALL_PROTECTION_ENABLED) {
                    relayState = false;
                    tipSafetyEnabled = false;

                    if (!SERIAL_DEBUG_MODE) {
                        digitalWrite(RELAY_PIN, LOW);
                        digitalWrite(HEAD_PIN, LOW);
                    }
                }
                
                loopContents = true;
            }
        }

        if (!loopContents) {
            vTaskDelay(pdMS_TO_TICKS(1));
        }
    }
}

// IMU Processing task for the BNO-08x
// Priority 2 | Core 0
void imuTask(void *params) {

    pidPitch.SetMode(AUTOMATIC);
    pidPitch.SetOutputLimits(-20, 20);
    pidPitch.SetSampleTime(10);

    // vTaskDelay(pdMS_TO_TICKS(3000));

    euler_t ypr;
    double filteredPitch = 0.0;

    while(1) {
        vTaskDelay(pdMS_TO_TICKS(10)); // 100 Hz
        imu.process_bno08x(&ypr);
        
        queueBin msg;
        filteredPitch = 0.5 * ypr.pitch + (1 - 0.5) * filteredPitch;
        pidIn = -1 * filteredPitch;
        pidSet = 0;
        pidPitch.Compute();
        msg.eulerY = -1 * filteredPitch;
        msg.pidOut = pidOut;
        msg.dX = 125.0 * tan(radians(pidOut));

        xQueueOverwrite(imuQueue, (void*) &msg);

        if (tipSafetyEnabled && abs(filteredPitch) > IMU_TIP_THRESHOLD && FALL_PROTECTION_ENABLED) {
            relayState = false;
            tipSafetyEnabled = false;

            if (!SERIAL_DEBUG_MODE) {
                digitalWrite(RELAY_PIN, LOW);
                digitalWrite(HEAD_PIN, LOW);
            }
        }
    }
}

// ==========================================================================
// Arduino Super Loop
// ==========================================================================

void setup() {
    
    // Basic hardware initialization
    delay(3000);

    pinMode(RELAY_PIN, OUTPUT);
    pinMode(HEAD_PIN, OUTPUT);

    Serial.begin(115200);
    servoSerial.begin(115200, SERIAL_8N1, 16, 17);

    // xQueue initialization
    imuQueue = xQueueCreate(1, sizeof(struct queueBin));
    serialQueue = xQueueCreate(512, sizeof(int));

    if (!servo.begin(serialQueue)) {
        while(1) {delay(1000); Serial.println("Servo2040 initialization failed");}
    }

    // Bluepad32 Setup
    BP32.setup(&onConnectedController, &onDisconnectedController);
    BP32.forgetBluetoothKeys();
    bd_addr_t controller_addr;
    sscanf_bd_addr(CTRL_MAC, controller_addr);
    uni_bt_allowlist_add_addr(controller_addr);
    uni_bt_allowlist_set_enabled(true);
    String fv = BP32.firmwareVersion();
    Serial.print("BP32 Firmware Version: ");
    Serial.println(fv);

    // To get the BD Address (MAC address) call:
    const uint8_t* addr = BP32.localBdAddress();
    Serial.print("BD Address: ");
    for (int i = 0; i < 6; i++) {
    Serial.print(addr[i], HEX);
    if (i < 5)
        Serial.print(":");
    else
        Serial.println();
    }

    // Config IMU if using BNO-08X
    if (IMU_CONFIG == BNO08x) {
        Serial.println("Using BNO08x IMU");
        if (!imu.begin()) {
            while(1) {delay(1000); Serial.println("IMU initialization failed");}
        }

        xTaskCreatePinnedToCore(imuTask, "imuTask", 8192, NULL, 2, &imuTaskHandle, 0);
    }

    // Configure PID
    pidPitch.SetMode(AUTOMATIC);
    pidPitch.SetOutputLimits(-20, 20);
    pidPitch.SetSampleTime(10);

    // FreeRTOS tasks
    xTaskCreatePinnedToCore(servoSerialTask, "serialTask", 10000, NULL, 3, &serialTaskHandle, 0);

    // Initialize action object 
    actions.begin(servo, imuQueue);

    // Send handshake message to Servo2040 to enable functionality
    queueSerial(0b01101001);

    // Blink the head LED to indicate end of setup sequence
    Serial.println("Ready!");
    digitalWrite(HEAD_PIN, HIGH);
    delay(500);
    digitalWrite(HEAD_PIN, LOW);
}

void loop() {

    BP32.update();

    for (int i = 0; i < BP32_MAX_GAMEPADS; i++) {
        ControllerPtr gamepad = myControllers[i];
        if (gamepad != nullptr) {
            gamepadProcessor(gamepad);
        }
    }

    vTaskDelay(pdMS_TO_TICKS(10));
}

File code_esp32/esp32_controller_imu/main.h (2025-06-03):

#ifndef MAIN_H
#define MAIN_H

#define VOLTAGE_CUTOFF  7.20

// PREAMBLES
#define RETURN_NONE 0x08
#define RETURN_VA   0x0F
#define RETURN_IMU  0b1001

// COMMAND CODES
#define CMD_PULSE       0x07
#define CMD_PULSE_DELAY 0x06
#define CMD_LED         0x02
#define CMD_ENABLE      0x0F
#define CMD_DISABLE     0x01
#define CMD_NONE        0x00

// COMMONLY USED SERO MASKS
#define ALL_SERVOS  0x1FFFF
#define LEG_SERVOS  0b1111111100000
#define RIGHT_ARM   0b11110
#define LEFT_ARM    0b11110000000011110

// SAFETY LOCK FOR FORWARD ROLL (X-BUTTON)
// SET TO TRUE TO PREVENT MISFIRES AND ACCIDENTS
#define ULT_LOCK true

// INT VALUE TO COMPARE AGAINST TO PERFORM MOVEMENT ACTIONS USING
// LEFT AND RIGHT JOYSTICKS
#define AXIS_THRESHOLD 400

// DISABLES RELAY ACTIVATION TO PREVENT SERVO ACTUATION.  INTENDED
// FOR USAGE WITH A SERIAL MONITOR FOR DEBUGGING PURPOSES
#define SERIAL_DEBUG_MODE false

#define IMU_TIP_THRESHOLD 30.0
#define FALL_PROTECTION_ENABLED true

struct servoStruct {
  int min;
  int mid;
  int max;
  bool angle180; // if false, will map to 270 angle range
};

struct queueBin {
  double eulerX;
  double eulerY;
  double eulerZ;
};

// If you're working with multiple robots, you can use this to select between
// devices and incorporate their respective calibration and controller mac
// addresses
enum DeviceID {E20A, C25A};
#define DEVICE_SELECT E20A

#if DEVICE_SELECT == E20A

  #define CTRL_MAC "98:b6:7f:0a:fa:59"

  servoStruct s_torso = {515, 1458, 2397, false};   // TORSO
  servoStruct s_ra1 =   {510, 1495, 2397, false};   // RIGHT ARM SHOULDER BASE
  servoStruct s_ra2 =   {543, 1505, 2413, false};   // RIGHT ARM SHOULDER SWING
  servoStruct s_ra3 =   {592, 1495, 2404, true};    // RIGHT ARM BICEP SWIVEL
  servoStruct s_ra4 =   {593, 1493, 2385, true};    // RIGHT ARM ELBOW
  servoStruct s_rl1 =   {592, 1512, 2405, true};    // RIGHT LEG THIGH
  servoStruct s_rl2 =   {588, 1490, 2372, true};    // RIGHT LEG FEMUR
  servoStruct s_rl3 =   {643, 1550, 2432, true};    // RIGHT LEG TIBIA
  servoStruct s_rl4 =   {587, 1493, 2405, true};    // RIGHT LEG ANKLE
  servoStruct s_la1 =   {505, 1457, 2409, false};   // LEFT ARM SHOULDER BASE
  servoStruct s_la2 =   {550, 1509, 2453, false};   // LEFT ARM SHOULDER SWING
  servoStruct s_la3 =   {622, 1530, 2480, true};    // LEFT ARM BICEP SWIVEL
  servoStruct s_la4 =   {622, 1533, 2440, true};    // LEFT ARM ELBOW
  servoStruct s_ll1 =   {597, 1500, 2410, true};    // LEFT LEG THIGH
  servoStruct s_ll2 =   {685, 1580, 2470, true};    // LEFT LEG FEMUR
  servoStruct s_ll3 =   {567, 1522, 2437, true};    // LEFT LEG TIBIA
  servoStruct s_ll4 =   {591, 1520, 2428, true};    // LEFT LEG ANKLE

#elif DEVICE_SELECT == C25A

  #define CTRL_MAC "98:b6:d5:20:65:22"

  servoStruct s_torso = {524, 1470, 2405, false};   // TORSO
  servoStruct s_ra1 =   {575, 1528, 2456, false};   // RIGHT ARM SHOULDER BASE
  servoStruct s_ra2 =   {542, 1522, 2420, false};   // RIGHT ARM SHOULDER SWING
  servoStruct s_ra3 =   {601, 1513, 2428, true};    // RIGHT ARM BICEP SWIVEL
  servoStruct s_ra4 =   {607, 1520, 2430, true};    // RIGHT ARM ELBOW
  servoStruct s_rl1 =   {653, 1558, 2451, true};    // RIGHT LEG THIGH
  servoStruct s_rl2 =   {597, 1530, 2440, true};    // RIGHT LEG FEMUR
  servoStruct s_rl3 =   {584, 1500, 2404, true};    // RIGHT LEG TIBIA
  servoStruct s_rl4 =   {560, 1486, 2389, true};    // RIGHT LEG ANKLE
  servoStruct s_la1 =   {561, 1520, 2440, false};   // LEFT ARM SHOULDER BASE
  servoStruct s_la2 =   {557, 1511, 2447, false};   // LEFT ARM SHOULDER SWING
  servoStruct s_la3 =   {602, 1514, 2413, true};    // LEFT ARM BICEP SWIVEL
  servoStruct s_la4 =   {615, 1537, 2456, true};    // LEFT ARM ELBOW
  servoStruct s_ll1 =   {555, 1488, 2398, true};    // LEFT LEG THIGH
  servoStruct s_ll2 =   {587, 1512, 2415, true};    // LEFT LEG FEMUR
  servoStruct s_ll3 =   {587, 1508, 2400, true};    // LEFT LEG TIBIA
  servoStruct s_ll4 =   {605, 1509, 2416, true};    // LEFT LEG ANKLE

#endif

// Pin mapping array for servos: 0th index = SERVO1, 17th index = SERVO18
servoStruct servoCluster[] = {
  s_torso, s_ra1, s_ra2, s_ra3, s_ra4,
  s_rl1, s_rl2, s_rl3, s_rl4,
  s_ll1, s_ll2, s_ll3, s_ll4,
  s_la1, s_la2, s_la3, s_la4,
  };
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

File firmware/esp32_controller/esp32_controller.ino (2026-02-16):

// ENDEAVOR HUMANOID ROBOT PROJECT
// ESP32 PRIMARY CONTROLLER
// Authored by ProtoDane

// This sketch provides the main functions for the Endeavor robot, providing controls
// via a Bluetooth controller, IMU functionality for fall detection and stability control,
// and servo actuation.

// Required Libraries
#include <uni.h>
#include <Bluepad32.h>
#include <PID_v1.h>
#include <Adafruit_BNO08x.h>

// Header files
#include "config.h"
#include "kinematics.h"
#include "servo2040.h"
#include "movesets.h"

// Bluepad32 instances
ControllerPtr myControllers[BP32_MAX_CONTROLLERS];

// BNO08x Setup (if being used)
HardwareSerial IMUSerial(1);
Adafruit_BNO08x bno08x(-1);

// GPIO Pins
#define RELAY_PIN 13
#define HEAD_PIN  12

// Control variables
bool operable = true;
bool enableBalancing = false;
volatile bool relayState = false;
volatile bool tipSafetyEnabled = false;

// PID
double Kp = 1.0; // go lower
double Ki = 0.0;
double Kd = 0.02;
double pidSet, pidIn, pidOut;
PID pidPitch(&pidIn, &pidOut, &pidSet, Kp, Ki, Kd, DIRECT);

// Dual core instances
TaskHandle_t h_taskSerialIn;
QueueHandle_t imuQueue;

// Container for passing data between Core 0 and Core 1 of the ESP32
struct queueBin {
  double eulerX;
  double eulerY;
  double eulerZ;
  double pidOut;
  double dX;
};



void getIMU(queueBin *q) {
  if (uxQueueMessagesWaiting(imuQueue) > 0) {
    xQueuePeek(imuQueue, q, 0);
  }
}

// Core1 task to process incoming UART messages from the Servo2040 (mainly IMU data)
void taskSerialIn(void *pvParameters) {
  
  pidPitch.SetMode(AUTOMATIC);
  pidPitch.SetOutputLimits(-20, 20);
  pidPitch.SetSampleTime(10);

  delay(5000);
  imuQueue = xQueueCreate(1, sizeof(struct queueBin));

  switch(IMU_CONFIG) {
    case IMU_DISABLED:
      Serial.println("No IMU selected");
      break;
    case IMU_055:
      Serial.println("BNO-055 Selected");
      process_bno055();
      break;
    case IMU_08X:
      Serial.println("BNO-08X Selected");
      process_bno08x();
      break;
  }
  while(1) {delay(10);}
}
  

void setup() {
  
  // Initialize GPIO
  pinMode(RELAY_PIN, OUTPUT);
  pinMode(HEAD_PIN, OUTPUT);
  
  // Initialize serial
  Serial.begin(115200);
  servoSerial.begin(115200, SERIAL_8N1, 16, 17);

  xTaskCreatePinnedToCore(taskSerialIn, "taskSerialIn", 10000, NULL, 1, &h_taskSerialIn, 1);
  delay(500);

  BP32.forgetBluetoothKeys();
  
  // Initialize Bluetooth allowlist
  bd_addr_t controller_addr;
  sscanf_bd_addr(CTRL_MAC, controller_addr);
  uni_bt_allowlist_add_addr(controller_addr);
  uni_bt_allowlist_set_enabled(true);

  String fv = BP32.firmwareVersion();
  Serial.print("Firmware version installed: ");
  Serial.println(fv);

  // To get the BD Address (MAC address) call:
  const uint8_t* addr = BP32.localBdAddress();
  Serial.print("BD Address: ");
  for (int i = 0; i < 6; i++) {
    Serial.print(addr[i], HEX);
    if (i < 5)
      Serial.print(":");
    else
      Serial.println();
  }

  // Bluepad32 initialization
  BP32.setup(&onConnectedController, &onDisconnectedController);

  if (SERIAL_DEBUG_MODE) {
    Serial.println("Serial debug mode!");
  } else {
    Serial.println("SERIAL DEBUG MODE DISABLED, DO NOT ACTIVATE SERVOS");
  }

  if (IMU_CONFIG == IMU_08X) {
    IMUSerial.begin(115200, SERIAL_8N1, 18, 19);
    if (!bno08x.begin_UART(&IMUSerial)) {
      Serial.println("Failed to find BNO08x chip");
      while(1) {delay(10);}
    }
    Serial.println("Found BNO08x chip!");
  }

  // Send handshake code to Servo2040
  servoSerial.write(0b01101001);
}

// Arduino loop function. Runs in CPU 1
void loop() {

  BP32.update();

  // It is safe to always do this before using the controller API.
  // This guarantees that the controller is valid and connected.
  for (int i = 0; i < BP32_MAX_CONTROLLERS; i++) {
    ControllerPtr myController = myControllers[i];

    if (myController && myController->isConnected()) {
      if (myController->isGamepad())
        mainProcess(myController);
    }
  }

  delay(10);
}

// Top level control structure to determine action sequences based on gamepad input
void mainProcess(ControllerPtr gamepad) {

  // Relay debounce variable; provides press/release action for toggling the relay


  // Check home button state and determine if a debounce action occurs and toggles the relay
  if (gamepad->miscSystem() & operable) {

    while(gamepad->miscSystem()) {BP32.update(); delay(50);}

    relayState = !relayState;

    if (!SERIAL_DEBUG_MODE) {
      digitalWrite(RELAY_PIN, !digitalRead(RELAY_PIN));
      digitalWrite(HEAD_PIN, !digitalRead(HEAD_PIN));
    }

    relayState ? cmdEnable() : cmdDisable();
  }

  // Check relay state and process the remaining gamepad controls if it is high
  if (relayState & operable) {

    // Fetch left/right joystick values
    int lx = gamepad->axisX();
    int ly = gamepad->axisY();
    int rx = gamepad->axisRX();
    int ry = gamepad->axisRY();
    
    // Check buttons first, then check drive controls last.  If no inputs, send idle command to servo driver
    if (gamepad->a()) {
      
      // Serial.println("[ESP32]: (B) pressed");
      tipSafetyEnabled = true;
      actionCrouch(gamepad);

    } else if (gamepad->b()) {

      // Serial.println("[ESP32]: (A) pressed");
      tipSafetyEnabled = true;
      actionSwipe(gamepad, false);
    
    } else if (gamepad->y()) {

      // Serial.println("[ESP32]: (X) pressed");
      if(!ULT_LOCK) {
        tipSafetyEnabled = false;
        actionRoll(gamepad);
        tipSafetyEnabled = true;
      }
    
    } else if (gamepad->x()) {

      // Serial.println("[ESP32]: (Y) pressed");
      tipSafetyEnabled = true;
      actionSwipe(gamepad, true);
    
    } else if (gamepad->dpad() & DPAD_UP) {

      // Serial.println("[ESP32]: DP-UP pressed");
      tipSafetyEnabled = true;
      actionEmote1(gamepad);
    
    } else if (gamepad->dpad() & DPAD_DOWN) {

      // Serial.println("[ESP32]: DP-DOWN pressed");
      //actionEmote2(gamepad);
      tipSafetyEnabled = true;
      actionEmote5(gamepad);

    } else if (gamepad->dpad() & DPAD_LEFT) {
    
      // Serial.println("[ESP32]: DP-LEFT pressed");
      tipSafetyEnabled = true;
      actionEmote3(gamepad);

    } else if (gamepad->dpad() & DPAD_RIGHT) {

      // Serial.println("[ESP32]: DP-RIGHT pressed");
      tipSafetyEnabled = true;
      actionEmote4(gamepad);
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

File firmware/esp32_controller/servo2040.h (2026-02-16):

// SERVO2040 HEADER FILE
// Authored by ProtoDane

// Functions and definitions used for communication with the Servo2040

#ifndef SERVO2040_H
#define SERVO2040_H

#include <HardwareSerial.h>
#include "config.h"
#include "kinematics.h"

// PREAMBLES
#define RETURN_NONE 0x08
#define RETURN_VA   0x0F
#define RETURN_IMU  0b1001

// COMMAND CODES
#define CMD_PULSE       0x07
#define CMD_PULSE_DELAY 0x06
#define CMD_LED         0x02
#define CMD_ENABLE      0x0F
#define CMD_DISABLE     0x01
#define CMD_NONE        0x00

// COMMONLY USED PIN MASKS
#define ALL_SERVOS  0x1FFFF
#define LEG_SERVOS  0b1111111100000
#define RIGHT_ARM   0b11110
#define LEFT_ARM    0b11110000000011110

// Static standing up pose
float idleAngles[] = {
  0.0, 
  -90.0, -60.0, 0.0, -20.0, 
  -4.0, -49.3, 31.2, -4.0, 
  4.0, 49.3, -31.2, 4.0, 
  90.0, 60.0, 0.0, 20.0
};

// UART Instance
HardwareSerial servoSerial(2);

// Data structure to hold info for a single servo
struct servoStruct {
  int min;
  int mid;
  int max;
  bool angle180; // if false, will map to 270 angle range
};

// Create servoStructs for each calibrated servo.  Rename the macro to your robot, same as in config.h
#if defined(ENDEAVOR)
  servoStruct s_torso = {515, 1458, 2397, false};   // TORSO
  servoStruct s_ra1 =   {510, 1495, 2397, false};   // RIGHT ARM SHOULDER BASE
  servoStruct s_ra2 =   {543, 1505, 2413, false};   // RIGHT ARM SHOULDER SWING
  servoStruct s_ra3 =   {592, 1495, 2404, true};    // RIGHT ARM BICEP SWIVEL
  servoStruct s_ra4 =   {593, 1493, 2385, true};    // RIGHT ARM ELBOW
  servoStruct s_rl1 =   {592, 1512, 2405, true};    // RIGHT LEG THIGH
  servoStruct s_rl2 =   {588, 1490, 2372, true};    // RIGHT LEG FEMUR
  servoStruct s_rl3 =   {643, 1550, 2432, true};    // RIGHT LEG TIBIA
  servoStruct s_rl4 =   {587, 1493, 2405, true};    // RIGHT LEG ANKLE
  servoStruct s_la1 =   {505, 1457, 2409, false};   // LEFT ARM SHOULDER BASE
  servoStruct s_la2 =   {550, 1509, 2453, false};   // LEFT ARM SHOULDER SWING
  servoStruct s_la3 =   {622, 1530, 2480, true};    // LEFT ARM BICEP SWIVEL
  servoStruct s_la4 =   {622, 1533, 2440, true};    // LEFT ARM ELBOW
  servoStruct s_ll1 =   {597, 1500, 2410, true};    // LEFT LEG THIGH
  servoStruct s_ll2 =   {685, 1580, 2470, true};    // LEFT LEG FEMUR
  servoStruct s_ll3 =   {567, 1522, 2437, true};    // LEFT LEG TIBIA
  servoStruct s_ll4 =   {591, 1520, 2428, true};    // LEFT LEG ANKLE

#elif defined(CONTENDER)
  servoStruct s_torso = {524, 1470, 2405, false};   // TORSO
  servoStruct s_ra1 =   {575, 1528, 2456, false};   // RIGHT ARM SHOULDER BASE
  servoStruct s_ra2 =   {542, 1522, 2420, false};   // RIGHT ARM SHOULDER SWING
  servoStruct s_ra3 =   {601, 1513, 2428, true};    // RIGHT ARM BICEP SWIVEL
  servoStruct s_ra4 =   {607, 1520, 2430, true};    // RIGHT ARM ELBOW
  servoStruct s_rl1 =   {653, 1558, 2451, true};    // RIGHT LEG THIGH
  servoStruct s_rl2 =   {597, 1530, 2440, true};    // RIGHT LEG FEMUR
  servoStruct s_rl3 =   {584, 1500, 2404, true};    // RIGHT LEG TIBIA
  servoStruct s_rl4 =   {560, 1486, 2389, true};    // RIGHT LEG ANKLE
  servoStruct s_la1 =   {561, 1520, 2440, false};   // LEFT ARM SHOULDER BASE
  servoStruct s_la2 =   {557, 1511, 2447, false};   // LEFT ARM SHOULDER SWING
  servoStruct s_la3 =   {602, 1514, 2413, true};    // LEFT ARM BICEP SWIVEL
  servoStruct s_la4 =   {615, 1537, 2456, true};    // LEFT ARM ELBOW
  servoStruct s_ll1 =   {555, 1488, 2398, true};    // LEFT LEG THIGH
  servoStruct s_ll2 =   {587, 1512, 2415, true};    // LEFT LEG FEMUR
  servoStruct s_ll3 =   {587, 1508, 2400, true};    // LEFT LEG TIBIA
  servoStruct s_ll4 =   {605, 1509, 2416, true};    // LEFT LEG ANKLE
#endif

// Pin mapping array for servos: 0th index = SERVO1, 17th index = SERVO18
// IT IS NOT RECOMMENDED THAT YOU MODIFY THIS ARRAY; THIS IS ALSO THE RECOMMENDED SERVO WIRING ORDER
servoStruct servoCluster[] = {
  s_torso, s_ra1, s_ra2, s_ra3, s_ra4,
  s_rl1, s_rl2, s_rl3, s_rl4,
  s_ll1, s_ll2, s_ll3, s_ll4,
  s_la1, s_la2, s_la3, s_la4,
};

// Send first byte packet of a message to the Servo2040.  First 4 bits are a preamble, last 4 bits are a command
void sendCommand(int preamble, int cmd) {
  servoSerial.write(preamble << 4 | cmd);
}

// Send pulse in microseconds as two bytes for a single servo channel
// FOR INTERNAL USE, DO NOT USE THIS FUNCTION FOR YOUR OWN CODE
void setServo(int pulse) {
  int first = pulse / 100;
  int second = pulse % 100;
  servoSerial.write(first);
  servoSerial.write(second);
}

// Maps the desired angle to the calibrated pulse.  angle180 used to differentiate between 180 and 270 deg servos
int mapPulse(float angle, float min, float mid, float max, bool angle180) {

  float maxAngle = angle180 ? 90.0 : 135.0;

  if (angle > 0.0) {

    return (int) (angle * (max - mid) / maxAngle + mid);

  } else if (angle < 0.0) {

    return (int) ((angle + maxAngle) * (mid - min) / maxAngle + min);

  } else {

    return mid;

  }
}

// Sets the servo cluster to the desired list of angles.  pinMask used to identify which servos are to be actuated
// NOTE1: LENGTH OF angles[] AND NUMBER OF BINARY 1'S IN pinMask ARE ASSUMED TO BE EQUAL
// NOTE2: THE BINARY ORDER OF pinMask FROM RIGHT TO LEFT CORRESPONDS TO THE SERVO CHANNELS ON THE SERVO2040 BOARD FROM SERVO1 TO SERVO18
void setServoCluster(float angles[], int pinMask) {
  
  int pIndex = 0; // angles array index (assumes array length and number of 1's in pinMask are equal)
  
  for (int i = 0; i < 18; i++) {

    uint32_t mask = 1 << i; // step forward mask by 1 bit

    if (pinMask & mask) { // true if i-th pinMask bit is equal to 1

      servoStruct servo = servoCluster[i];
      int calibratedPulse = mapPulse(angles[pIndex], servo.min, servo.mid, servo.max, servo.angle180);
      setServo(calibratedPulse);
      pIndex++;

    } else {

      // Set servo to an out of range pulse; will be ignored by Servo2040
      setServo(1);
    
    }
  }
}
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

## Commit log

2025-06-03 Added servo calibration files and made a few updates to the README files
    [ServoCalibrationJig.step, ServoDial.stl, ServoMount.stl]
2025-06-03 Fixed small syntax errors in servo calibration readme
2025-06-03 Adding servo2040 and esp32 code. Currently not in a usable state; commit was made to back up project files to the repository
2025-06-03 Renamed servo2040_peripheral to servo2040_client to be more concise
2025-06-03 Readme file updated to reflect added material
2025-06-03 Fixing Servo2040 startup issues, added new emote sequence to ESP32
    [main.h, servo2040_client.cpp]
2025-06-03 Began IMU integration. Nothing much, just copied over the servo2040 basic client for now.
2025-06-03 Added serial debug mode; IMU readouts by the ESP32 confirmed to be working as well.
2025-06-03 Prev commit didn't stage latest changes
    [esp32_controller_imu.ino, main.h]
2025-06-03 Checkpoint before reworking IMU controller to minimize blocking processes
    [esp32_controller_imu.ino, main.h]
2025-06-03 IMU data now sent to ESP32 after handshake message is received. ESP32 reads IMU data, which is stored in queue or used to trigger fall safety shutoff
2025-06-28 First commit of dynamic balancing ESP32 controller. PID parameters overshooting, but it's at least trying to reach the equilibrium setpoint
    [config.h, servo2040.h]
2025-07-02 Checkpoint commit with functional standing stability
    [config.h, servo2040.h]
2025-07-18 Added IMU flags to control depending on the sensor model or lack thereof
2025-07-18 Removed BNO08x pico library, decided to use UART on ESP32
2025-09-02 Added CAD model
2026-02-16 Refactored ESP32 stack to PlatformIO
2026-02-20 File restructuring
    [EndeavorII-v1.step, ServoCalibrationJig.step, ServoDial.stl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]
